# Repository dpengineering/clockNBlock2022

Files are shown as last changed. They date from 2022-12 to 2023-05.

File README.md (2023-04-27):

# ToDo List
[Google Doc Link](https://docs.google.com/document/d/1s_93HzQu_74fJWDLWwISt_NYs3OvQ41pf5nRqQ8sUA4/edit?usp=sharing).  
Please request access if you would like to change the doc or check things off.  

# ClockNBlock 2022 Version
Written by `@ArnavVWadhwa` and `@bvesper15` this is the new version of the clockNBlock project with the "shiny new delta arm." The major changes this year was to the circuit boards used. We added `@Stan-Reifel's` new DPi Circuit boards and redid the wiring. 
  
The code is also completely brand new and this is the third version of the code I have written. I hope it holds up to a good standard.

For any questions with the project feel free to reach out me.  
Arnav Wadhwa:  
(805) 570-5030.   
arnav.v.wadhwa@gmail.com

Note: When you contact me please let me know who you are and that this is for the clock and block so I don't accidently ignore you.

Here is the fun story for the project.
# It Clocks! It Blocks! New and improved only at Faker Maire!

# A Tale of Two Arms

This is the repository for the redesigned ClockNBlocks. The ClockNBlocks is a project in which a robotic arm stacks block towers, and sweeping clock hands susequently knock over the towers.

The project was first developed in the 2016-17 school year, employing a gantry-style serial manipulator arm. It wasn't fast; it wasn't elegant, but in ran like a beauty. The code for this version of the project was perfected by `@jproney` himself in the fall of 2017, and can be found here: https://github.com/dpengineering/ClockNBlockHW

After `@jproney's` labors to perfect the CNB, the original project was torn apart, and the slow, sturdy gantry arm replaced with a shiny new Delta Robot. What is a Delta Robot you ask? Luckily for you, `@jproney` made https://github.com/dpengineering/DeltaArm to answer this age old question. The DeltaArm repository contains the Inverse Kinematic and Forward Kinematic equations for controlling the new Delta Arm.

But that's not where the story ends. The original ClockNBlock was powered by an artificial brain known as the R-dwino (sometimes stylized _Arduino_). However, the new arm was to be controlled by a Pi of Raspberry and it's trusty companion, the Engine of Slush. Therefore, it became necessary for the Arduinos controlling the project's pneumatic actuators to communicate with the Rasperry Pi. To accomplish this task, `@jproney` created https://github.com/dpengineering/PythonManager by standing of the shoulders of `@jmgrosen`, the hero who first brought peace to Mechatronica. Unfortunately,
PythonManager was developed quite hastily, and is currently rather messy and confusing. 

And now that brings us here. The repository you are viewing combines the DeltaArm, PythonManager, and old ClockNBlockHW repositiories to create ClockNBlockPi. In its current state, the ClockNBlock runs, but not well. The arm control software (forward/inverse kinematics) works quite well, but for one reason or another the arm struggles to maintain the sub-inch precision required to pick up blocks consistently. This is likely due to backlash in the arm transmissions, slippage in shaft couplers, and inconsistencies in the homing of the arm.

Now you come into the story, young squire. Your task is to tame the Arm of Delta, build the Block Towers high once more, and bring the ClockNBlock back to its golden age. Godspeed.

Sincerely,
James "Petey/Stagflation/jproney" Roney

P.S. I did most (all) of these - Arnav

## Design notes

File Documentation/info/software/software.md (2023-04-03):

# Software

The software has been written in an object-oriented style because I am a Java guy
and this is how I code. Feel free to change this though.  

## State Machine
All the components have what are called state-machines. This eliminates the need for small loops and allows
for constant checking of each object. Every state in the state machine has three components:  

#### Do something  
This happens on the first time the state is called and is the main portion of the state.  
After this state is hit, a newState flag is set to false and the rest of the times this state is reached
it will

#### Wait for something
This is pretty self-explanatory. It waits for a set amount of time or until some condition is reached.

#### Set a new state
The state machine moves onto a different state and the newState flag is reset to True because 
we are in a new state.

There are four main objects that talk to each other.

## Robot Arm
This holds all the objects because it has to talk to everything.  
This controls the robot arm and holds the states for it. Essentially, the robot arm is continuously asking the block manager what it should be doing
and goes to pick up and place blocks. When it has nothing to do, it will just home itself and wait.  

## Block Manager
The block manager isn't actually a physical part, it is just there to tell the robot what it should be doing.  
It holds the positions of the blocks to be placed in a list and the count of which block the robot is on.  
This means that there are no sensors to check if the robot has actually stacked the block or if someone has messed with the stack.

## Clock
The clock either runs as a regular clock or the minute hand moves fairly quickly and the hour hand points to where the robot is going next.
The real time mode currently doesn't really make sense as the project doesn't have a clock face. Also, it's way too slow.  
  
The clock's state machine is fairly simple. Either the clock just goes at real time or the minute hand goes at a set speed and the hour hand asks the robot where it should go
(Actually, the robot arm just tells the hour hand where to go, but this is essentially the same thing)

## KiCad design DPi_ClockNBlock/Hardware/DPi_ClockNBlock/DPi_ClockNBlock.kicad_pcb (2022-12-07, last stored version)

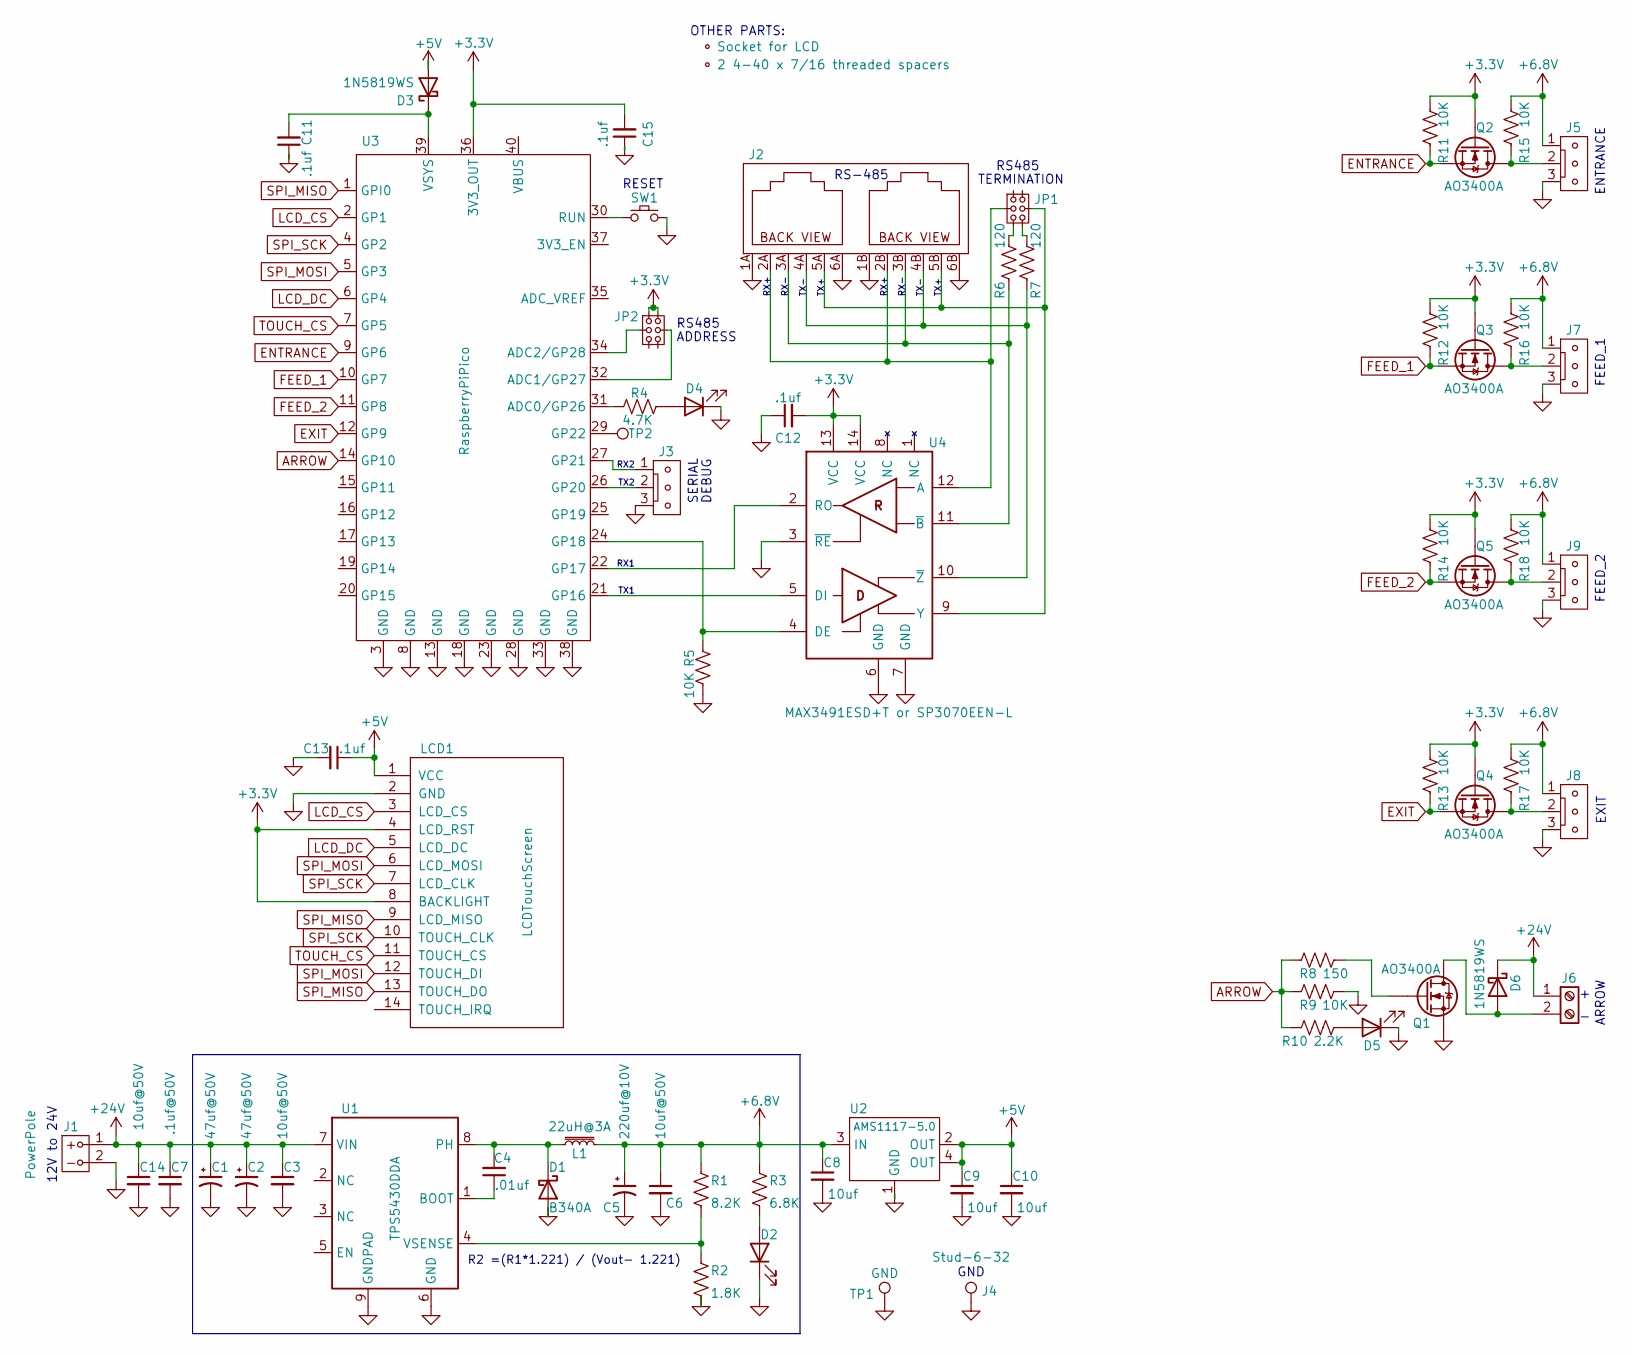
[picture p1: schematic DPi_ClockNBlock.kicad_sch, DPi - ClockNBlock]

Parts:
AP1: Socket for LCD
AP2: 2 4-40 x 7/16 threaded spacers
C1, C2: 47uf@50V; CP_Elec_6.3x7.7
C3, C6, C14: 10uf@50V; C_0805_2012Metric
C4: .01uf; C_0805_2012Metric
C5: 220uf@10V; CP_Elec_6.3x7.7
C7: .1uf@50V; C_0805_2012Metric
C8, C9, C10: 10uf; C_0805_2012Metric
C11, C12, C13, C15: .1uf; C_0805_2012Metric
D1: B340A; D_SMA
D2, D4, D5: RED LED; LED_0805_2012Metric
D3, D6: 1N5819WS; D_SOD-323
J1: PowerPole2
J2: 6P6C_Modular_Dual
J3, J5, J7, J8, J9: Molex-Vert-3-L; Molex-Vert-3
J4: Stud-6-32; ThreadedStud_6-32-375
J6: ScrewTerminal3.5MM-2
JP1, JP2: Jumper3x2
L1: 22uH@3A; Inductor_6.6x7.1_H3
LCD1: LCDTouchScreen
Q1, Q2, Q3, Q4, Q5: AO3400A; SOT-23
R1: 8.2K; R_0805_2012Metric
R2: 1.8K; R_0805_2012Metric
R3: 6.8K; R_0805_2012Metric
R4: 4.7K; R_0805_2012Metric
R5, R9, R11, R12, R13, R14, R15, R16, R17, R18: 10K; R_0805_2012Metric
R6, R7: 120; R_0805_2012Metric
R8: 150; R_0805_2012Metric
R10: 2.2K; R_0805_2012Metric
SW1: PushButton_C318884
TP1: GND; TestPoint
TP2: GP22; TestPoint
U1: TPS5430DDA; TI_SO-PowerPAD-8_ThermalVias
U2: AMS1117-5.0; SOT-223
U3: RaspberryPiPico
U4: MAX3491ESD+T or SP3070EEN-L; SOIC-14_3.9x8.7mm_P1.27mm

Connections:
+3V3: C12.2, C15.2, JP2.1, JP2.2, LCD1.4 (LCD_RST), LCD1.8 (BACKLIGHT), Q2.1 (G), Q3.1 (G), Q4.1 (G), Q5.1 (G), R11.2, R12.2, R13.2, R14.2, U3.36 (3V3_OUT), U4.13 (VCC), U4.14 (VCC)
+5V: C9.1, C10.1, C13.1, D3.2 (A), LCD1.1 (VCC), U2.2 (OUT), U2.4 (OUT)
+6.8V: C5.1, C6.1, C8.1, J5.1, J7.1, J8.1, J9.1, L1.2, R1.1, R3.1, R15.2, R16.2, R17.2, R18.2, U2.3 (IN)
+24V: C1.1, C2.1, C3.1, C7.1, C14.1, D6.1 (K), J1.1, J6.1, U1.7 (VIN)
ARROW: R8.1, R9.1, R10.1, U3.14 (GP10)
ENTRANCE: Q2.2 (S), R11.1, U3.9 (GP6)
EXIT: Q4.2 (S), R13.1, U3.12 (GP9)
FEED_1: Q3.2 (S), R12.1, U3.10 (GP7)
FEED_2: Q5.2 (S), R14.1, U3.11 (GP8)
GND: C1.2, C2.2, C3.2, C5.2, C6.2, C7.2, C8.2, C9.2, C10.2, C11.1, C12.1, C13.2, C14.2, C15.1, D1.2 (A), D2.1 (K), D4.1 (K), D5.1 (K), J1.2, J2.1A, J2.1B, J2.6A, J2.6B, J3.3, J4.1, J5.3, J7.3, J8.3, J9.3, LCD1.2 (GND), Q1.2 (S), R2.2, R5.2, R9.2, SW1.2, TP1.1, U1.6 (GND), U1.9 (GNDPAD), U2.1 (GND), U3.3 (GND), U3.8 (GND), U3.13 (GND), U3.18 (GND), U3.23 (GND), U3.28 (GND), U3.33 (GND), U3.38 (GND), U4.3 (~RE), U4.6 (GND), U4.7 (GND)
LCD_CS: LCD1.3 (LCD_CS), U3.2 (GP1)
LCD_DC: LCD1.5 (LCD_DC), U3.6 (GP4)
unnamed: C4.1, U1.1 (BOOT)
unnamed: C4.2, D1.1 (K), L1.1, U1.8 (PH)
unnamed: C11.2, D3.1 (K), U3.39 (VSYS)
unnamed: D2.2 (A), R3.2
unnamed: D4.2 (A), R4.2
unnamed: D5.2 (A), R10.2
unnamed: D6.2 (A), J6.2, Q1.3 (D)
unnamed: J2.2A, J2.2B, JP1.3, U4.12 (A)
unnamed: J2.3A, J2.3B, R6.1, U4.11 (~B)
unnamed: J2.4A, J2.4B, R7.1, U4.10 (~Z)
unnamed: J2.5A, J2.5B, JP1.4, U4.9 (Y)
unnamed: J3.1, U3.27 (GP21)
unnamed: J3.2, U3.26 (GP20)
unnamed: J5.2, Q2.3 (D), R15.1
unnamed: J7.2, Q3.3 (D), R16.1
unnamed: J8.2, Q4.3 (D), R17.1
unnamed: J9.2, Q5.3 (D), R18.1
unnamed: JP1.5, R6.2
unnamed: JP1.6, R7.2
unnamed: JP2.3, U3.34 (ADC2/GP28)
unnamed: JP2.4, U3.32 (ADC1/GP27)
unnamed: Q1.1 (G), R8.2
unnamed: R1.2, R2.1, U1.4 (VSENSE)
unnamed: R4.1, U3.31 (ADC0/GP26)
unnamed: R5.1, U3.24 (GP18), U4.4 (DE)
unnamed: SW1.1, U3.30 (RUN)
unnamed: TP2.1, U3.29 (GP22)
unnamed: U3.21 (GP16), U4.5 (DI)
unnamed: U3.22 (GP17), U4.2 (RO)
SPI_MISO: LCD1.9 (LCD_MISO), LCD1.13 (TOUCH_DO), U3.1 (GPI0)
SPI_MOSI: LCD1.6 (LCD_MOSI), LCD1.12 (TOUCH_DI), U3.5 (GP3)
SPI_SCK: LCD1.7 (LCD_CLK), LCD1.10 (TOUCH_CLK), U3.4 (GP2)
TOUCH_CS: LCD1.11 (TOUCH_CS), U3.7 (GP5)

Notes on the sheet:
SERIAL
TERMINATION
TX2
RX2
RX-
RESET
EXIT
TX+
RS-485
RX1
GND
ENTRANCE
12V to 24V
TX-
DEBUG
RS485
OTHER PARTS:
FEED_1
RX+
TX1
R2 =(R1*1.221) / (Vout- 1.221)
ADDRESS
ARROW
FEED_2

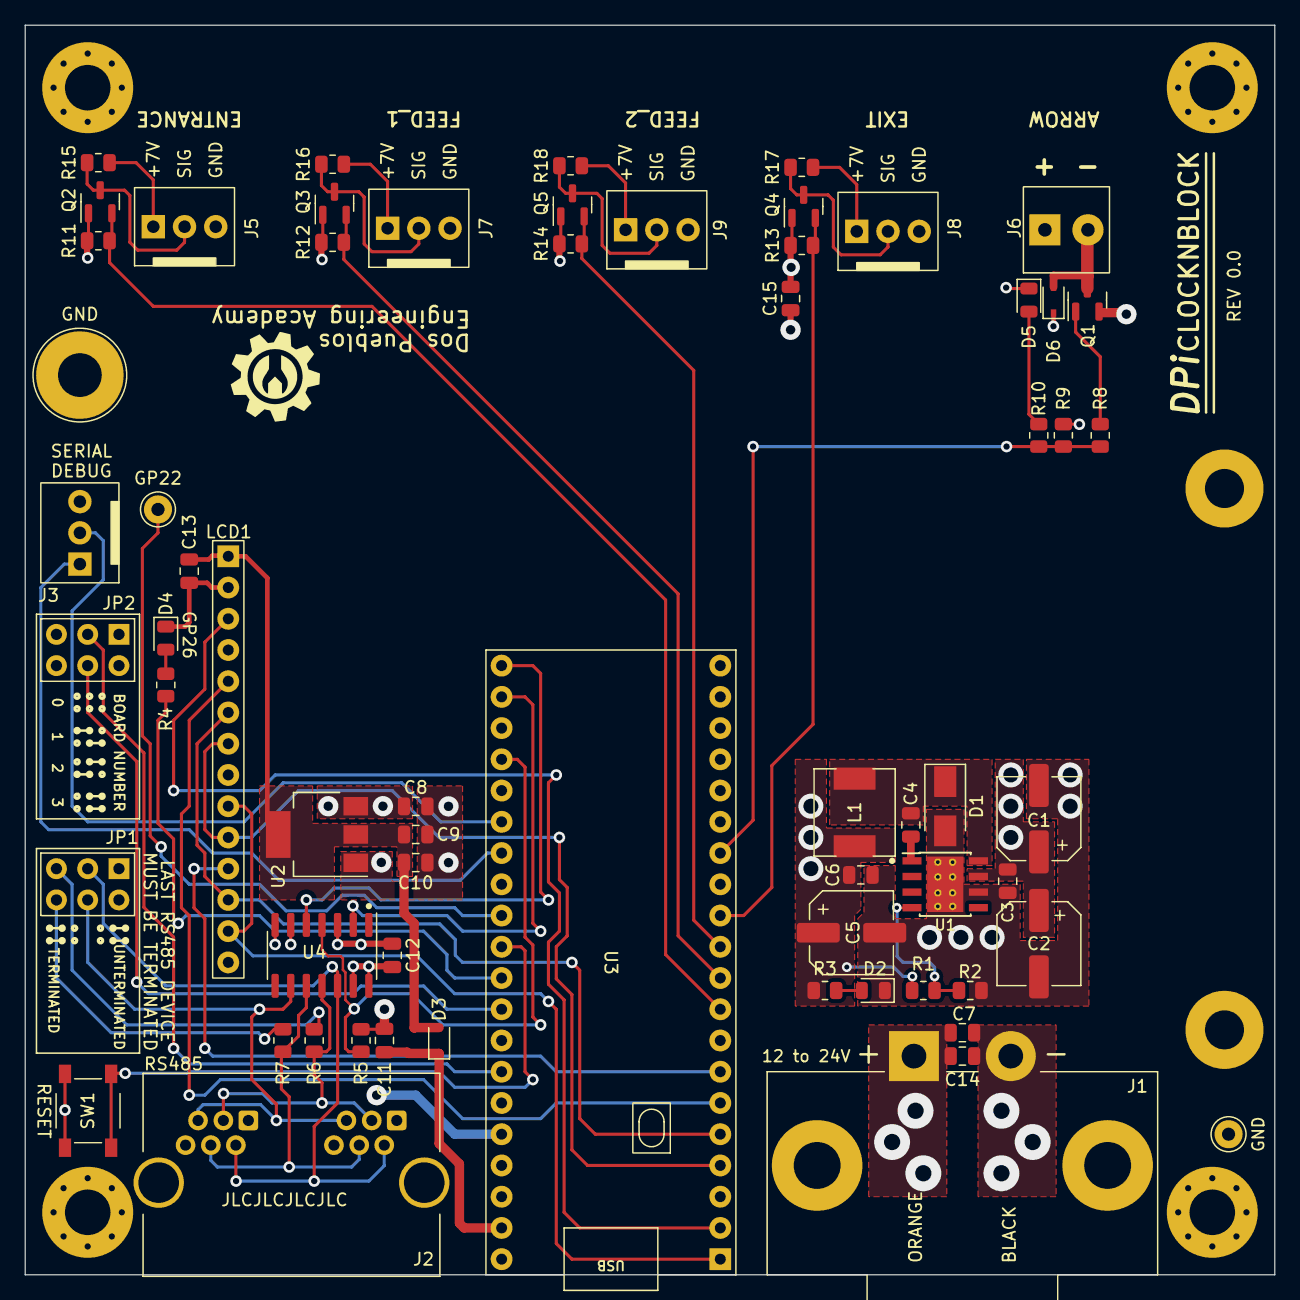
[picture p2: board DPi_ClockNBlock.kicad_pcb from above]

Board: 4 copper layers, 101.6 x 101.6 mm, 64 parts (0 on the bottom side), 45 nets.

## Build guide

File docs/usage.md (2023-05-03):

# Usage

### Spark Notes:
To run the machine, turn it on and if there are blocks
in the entrance of all the feeders, it will run in personality mode, otherwise it will
run in the regular mode.

### File Structure:  

The project is structured like this:  
```
startup.py 
imbuingPersonality/
    main.py
    *Other files*

regularMoves/
    main.py
    *Other files*
```
startup.py will choose which version of the code to run.  
Currently, this file is stored within this repo, the structure
looks like the one above on the RPi though.  

### Running the machine:
Basically just watch it do its thing, if anything scary happens or a catastrophic failure happens,
press the big red E-STOP button and swear at me. I hope this never happens.

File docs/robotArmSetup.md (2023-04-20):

# Setting Constants and Variables in DPi Robot board

### *TBD when working on the ChladniPlate*

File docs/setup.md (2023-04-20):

# Setup

This project has 3 main components: the robot arm, the cloc, and the feeders.  
  
### Robot Arm
The robot arm has the most moving parts and has the most setup required for it.  
The robot is a delta arm which is controlled by the [DPi_Robot](https://github.com/dpengineering/DPi_Robot) board.  
  
The first thing that needs to be set up are the constants held in the robot board itself.  
To do this, connect your computer to the raspberry pi and run a program such as the LinearDeltaRobotSetup.py. Our constants are all held
in that file and on the DPi_Robot board itself through its menus. Use the touchscreen on the board to access those.  
Also, go through and test each motor, limit switch, homing method, driver type, and the dip switches on the motor drivers.  
Dip switches set current limits and microstepping. Switches **a, b, c, d** should be down.  
Detailed Setup Guide for constants: [Robot Arm Setup](robotArmSetup.md)

Next, important points need to be set up on the robot arm. These points are the home position, the position where the arm is ready to pick up a block, and the position where the arm is ready to place a block.  
The home is already set as it is just where the robot goes to hit the limit switches. And the coordinate system we use is the Robot Coordinates. 
The robot can speak in 2 different coordinate systems: Robot Coordinates and Human Coordinates. 
Robot coordinates are the coordinates that the robot actually uses to move places. The Human Coordinates can be configured 
to have (0, 0, 0) to be wherever you want it to be. Currently, the Human Coordinates are the exact same as the robot coordinates.  
  
Next you will have to train all the points. There is a program, trainRobotJoystick.py that will allow you to use one of the DPEA's joysticks
Then, drive the robot around to the pick-up locations and verify that the robot can actually pick up the block and save that location. 
Next, drive the robot to the place locations (the spot where the robot will place the block that is closest to the center of the machine) verify that the hour hand cannot hit the 
arm or the block when the robot is in that position. Rember that the robot head has a width and can hit the hour hand. In this case, the robot will not lose steps but the hour hand will.  
The button controls are outlined in the check_other_buttons() method in the trainRobotJoystick.py file.   

Finally verify which solenoid controlls the magnet and which one controls the rotation.

### Clock
The clock doesn't require too much setup. The only thing that needs to be setup is the 12:00 position.  
To do this, home the clock which will have the hands at some random position, then drive the clock hands to the 12:00 position (wherever you choose that to be preferably over one of the build locations).  
  
The minute hand has about a 204:1 gear reduction. This is not exact so find how many steps are needed for one full rotation  
The hour hand has a 5:1 gear reduction. This should be exact, but is a good idea to verify that.

### Feeders

The feeders are a pain.  
To start, find which solenoid corresponds to the piston that pushes to the side or up for each feeder.  
Hopefully this has not changed. Then, check how fast each piston pushes the block.  
For the side pistons, this should be fairly fast, but not too fast as the piston will just destroy itself.  
The up pistons should be as fast as possible such that the block does not 'jump' when it stops at the top. The block should not leave the 
detection of the sensor at the top.  
Next, calibrate each sensor with the potentiometer screw at the bottom of the sensor. Place a block in a place where the sensor should trigger,
then make sure the sensor is triggered, the light at the bottom should show that. And make sure the sensor is not too sensitive to where it gives false positives.  
You will need to pull each feeder out to adjust some of the sensors. This is outlined in the Hardware portion of the docs.

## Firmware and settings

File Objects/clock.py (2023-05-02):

from time import sleep, localtime
from dpeaDPi.DPiStepper import DPiStepper


class Clock:
    # Constants
    dpiStepper = DPiStepper()

    # Motor Constants
    MICROSTEPPING = 8

    HOUR_HAND_PIN = 0
    HOUR_HAND_GEAR_REDUCTION = 5  # Gear reduction is 5:1
    # I am not sure why there is 300 extra steps for a full rotation.
    HOUR_HAND_STEPS_PER_REVOLUTION = 200 * MICROSTEPPING * HOUR_HAND_GEAR_REDUCTION + 290  # 8300
    # Hour hand base speed, 1 revolution in 12 hours, about 0.19 steps per second
    HOUR_HAND_BASE_SPEED = HOUR_HAND_STEPS_PER_REVOLUTION / (12 * 60 * 60)
    # Hour hand max speed. I don't feel comfortable sending it more than 0.5 rev / sec - 4150 steps/sec
    HOUR_HAND_MAX_SPEED = int(HOUR_HAND_STEPS_PER_REVOLUTION / 2)
    HOUR_HAND_ACCELERATION = HOUR_HAND_MAX_SPEED // 4

    # Hour Hand offset, not sure why this is needed...
    HOUR_HAND_OFFSET = 6.3  # degrees

    MINUTE_HAND_PIN = 1
    MINUTE_HAND_GEAR_REDUCTION = 204  # Gear reduction is 204:1
    MINUTE_HAND_STEPS_PER_REVOLUTION = int(200 * MICROSTEPPING * MINUTE_HAND_GEAR_REDUCTION * 1.002)  # 326400
    # Base minute hand speed, 1 revolution per hour, about 90.6 steps per second
    MINUTE_HAND_BASE_SPEED = MINUTE_HAND_STEPS_PER_REVOLUTION / (60 * 60)
    MINUTE_HAND_MAX_SPEED = 20000
    MINUTE_HAND_ACCELERATION = MINUTE_HAND_MAX_SPEED // 4

    # TODO: Ask Stan what's up with this

    def __init__(self):
        self.initialize()
        self.robotIdleFlg = False

    def initialize(self):

        self.dpiStepper.setBoardNumber(0)
        if not self.dpiStepper.initialize():
            raise Exception("DPi Stepper initialization failed")

        self.dpiStepper.setMicrostepping(self.MICROSTEPPING)

        self.dpiStepper.enableMotors(True)

    def setup(self):
        """ Sets up the hands so they can be used."""

        # Set accelerations
        # this is done once and left alone
        self.dpiStepper.setAccelerationInStepsPerSecondPerSecond(self.HOUR_HAND_PIN, self.HOUR_HAND_ACCELERATION)
        self.dpiStepper.setAccelerationInStepsPerSecondPerSecond(self.MINUTE_HAND_PIN, self.MINUTE_HAND_ACCELERATION)

        # Home hands
        self.dpiStepper.moveToHomeInSteps(self.HOUR_HAND_PIN, 1, self.HOUR_HAND_MAX_SPEED,
                                          self.HOUR_HAND_STEPS_PER_REVOLUTION)

        self.dpiStepper.moveToHomeInSteps(self.MINUTE_HAND_PIN, 1, self.MINUTE_HAND_MAX_SPEED,
                                          self.MINUTE_HAND_STEPS_PER_REVOLUTION)

        while not self.dpiStepper.getAllMotorsStopped():
            sleep(0.1)

        # Move to 12:00 position
        self.setSpeeds(self.HOUR_HAND_MAX_SPEED, self.MINUTE_HAND_MAX_SPEED)

        self.dpiStepper.moveToRelativePositionInSteps(self.HOUR_HAND_PIN, 2025, False)
        self.dpiStepper.moveToRelativePositionInSteps(self.MINUTE_HAND_PIN, -81100, False)

        while not self.dpiStepper.getAllMotorsStopped():
            sleep(0.1)

        self.dpiStepper.setCurrentPositionInSteps(self.HOUR_HAND_PIN, 0)
        self.dpiStepper.setCurrentPositionInSteps(self.MINUTE_HAND_PIN, 0)

        return True

    # This is necessary because the block feeders need to prime which means the clock needs to be out of the way
    # After that happens we can go to real time.
    def setup2(self):
        """ Sets up the hands so they can be used."""

        # Set minute hand speed to max
        self.dpiStepper.setSpeedInStepsPerSecond(self.MINUTE_HAND_PIN, self.MINUTE_HAND_MAX_SPEED)
        # Send minute hand in a full circle
        self.dpiStepper.moveToRelativePositionInSteps(self.MINUTE_HAND_PIN, self.MINUTE_HAND_STEPS_PER_REVOLUTION, True)
        # Move to current time
        t = localtime()
        hourToSteps, minuteToSteps = self.convertTimeToSteps(t.tm_hour, t.tm_min, t.tm_sec)
        print(f'Hour: {t.tm_hour}, Minute: {t.tm_min}, Second: {t.tm_sec}')
        print(f'Hour Steps: {hourToSteps}, Minute Steps: {minuteToSteps}')
        self.moveToPositionsRelative(hourToSteps, minuteToSteps, waitFlg=True)
        print(f'Finished moving to current time')
        print(f'Current Hour Position: {self.dpiStepper.getCurrentPositionInSteps(self.HOUR_HAND_PIN)}')
        print(f'Target Hour Position: {hourToSteps}')

        # Set base speeds
        print(self.setSpeeds(self.HOUR_HAND_BASE_SPEED, self.MINUTE_HAND_BASE_SPEED))
        print(f'Minute Hand Base Speed: {self.MINUTE_HAND_BASE_SPEED}')

        # Set minute hand going for a revolution
        # self.moveToPositionsRelative(minuteHandPosition=self.MINUTE_HAND_STEPS_PER_REVOLUTION)

        return True

    def process(self):
        """Processes the clock"""
        # This just basically includes checking how far off from the desired position the hands are
        # if they are too far away, then speed/slow them down to get them back to the desired position

        # Note: One case where this will be off is when there is a transfer from 11:59 to 12:00
        # or something along those lines. However, this will be fixed fairly quickly because it will only speed up for around
        # 1 second and then slow down again. This needs to be tested though

        # Get current time
        t = localtime()
        hourToSteps, minuteToSteps = self.convertTimeToSteps(t.tm_hour, t.tm_min, t.tm_sec)
        hourToSteps = hourToSteps % self.HOUR_HAND_STEPS_PER_REVOLUTION
        minuteToSteps = minuteToSteps % self.MINUTE_HAND_STEPS_PER_REVOLUTION


        # Get current positions
        _successFlg, hourPosition = self.dpiStepper.getCurrentPositionInSteps(self.HOUR_HAND_PIN)
        hourPosition = hourPosition % self.HOUR_HAND_STEPS_PER_REVOLUTION
        _successFlg, minutePosition = self.dpiStepper.getCurrentPositionInSteps(self.MINUTE_HAND_PIN)
        minutePosition = minutePosition % self.MINUTE_HAND_STEPS_PER_REVOLUTION

        # Calculate the difference between the desired position and the current position
        hourDifference = hourToSteps - hourPosition
        minuteDifference = minuteToSteps - minutePosition

        # If there is a difference in the hour hand, send it to the desired position
        if hourDifference != 0:
            # print(f'Hour hand is off by {hourDifference} steps')
            self.dpiStepper.moveToRelativePositionInSteps(self.HOUR_HAND_PIN, hourDifference, False)


        if minuteDifference != 0:
            # print(f'Minute hand is off by {minuteDifference} steps')
            self.dpiStepper.moveToRelativePositionInSteps(self.MINUTE_HAND_PIN, minuteDifference, False)


    #--------------------------------    Helper functions    --------------------------------#
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

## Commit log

2022-11-04 set up constants to initalize the linear delta arm
2022-11-07 Organized files and made a test for the robot arm
2022-11-07 Added debugging prints
2022-11-28 Added DPiClockNBlock driver python file
2022-12-05 Updated homing function in clockHands
2022-12-08 Fixed clock alignment, changed initial setup to allow robot arm to move further down, added solenoid information
2022-12-08 Moved Stan's DPi_ClockNBlock directory to the correct git repo
    [DPi_ClockNBlock-JLCPCB-BOM.csv, DPi_ClockNBlock.kicad_pcb, DPi_ClockNBlock.kicad_sch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]
2022-12-09 added easier training feature for robot arm
2022-12-09 specified drivers for solenoids
2022-12-09 fixed solenoid driver numbers and changed movement for testing
2022-12-09 moved print statement
2022-12-09 print stuff
2022-12-13 added state function for arm
2022-12-15 Worked on logic to move robot arm
2022-12-15 First draft of robot arm logic
2022-12-27 Resturctured files and updated state functions for robot arm
2023-01-04 adding prints
2023-01-11 Debugging jerky robot arm mobe
2023-02-24 debugging robot arm
2023-04-05 Refactoring code and starting to give personality to the robot arm
2023-04-06 Fixed cartesianToPolar and added a small robot arm test
    [clock.py]
2023-04-06 updated button placements
2023-04-07 Feeders, clock need testing, robot arm, manager need to be finished
2023-04-13 Debugging and adding print statements. Debugging RobotManager and adding print statements to clock and main
2023-04-13 Removing print statement. Debug with the actual debugger now...
2023-04-24 debugged, need to fix ZigZag and hour hand
    [clock.py]
2023-04-26 Debugged zigZag move, might need a check to avoid running into the posts
    [clock.py]
2023-05-04 Updated homing every 5 minutes
